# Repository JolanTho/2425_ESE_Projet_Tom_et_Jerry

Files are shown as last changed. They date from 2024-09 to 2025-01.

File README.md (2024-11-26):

# 2425_ESE_Tom&Jerry

## Sommaire
- [Présentation](#présentation)
- [Mécanique](#1-mécanique)
- [Électronique](#2-électronique)
- [Informatique](#3-informatique)
- [Stratégies](#4-stratégies)
- [Installation](#installation)
- [Contribution](#contribution-)
- [Auteurs et Contact](#auteurs-)

---

## Présentation

>Bienvenue sur le dépôt GitHub de **Tom&Jerry**. Ce projet a pour but de développer un robot autonome qui sur un plan plat joue à chat. Le plan est sans rebord, les matchs de 60secondes et le robot change de rôle (Chat/Souris) lors des contacts avec le(s) autre(s) robot(s).

>Ce projet est organisé en trois sous-domaines principaux :
>* **Mécanique** : Conception et fabrication des structures et composants mécaniques.
>* **Électronique** : Conception des circuits électroniques et sélection des composants.
>* **Informatique** : Développement du logiciel et de l'algorithme pour le contrôle du système.
>* **Stratégies** : Focus sur les stratégies mises en place pour s'échapper ou capturer.

---

## Détails du Projet

### 1. Mécanique
>Cette section est dédiée à la conception et à la fabrication des parties mécaniques du projet. 

#### Description :
- **Modélisation CAO** : Les pièces du projet ont été modélisées en utilisant **OnShape**.
- **Matériaux** : Les matériaux utilisés incluent **Plastique PLA, ...**.
- **Assemblage** : Le système est assemblé à l’aide de **(ex. vis, écrous, etc.)** et monté selon les plans fournis dans le dossier **/mechanical_drawings**.

#### Fichiers et Dossiers :
>* **/mechanical_drawings/** : Contient les fichiers CAO et les plans techniques.
>* **/materials_list.txt** : Liste des matériaux et composants utilisés.

---

### 2. Électronique
>Cette partie couvre la conception et le développement des circuits électroniques nécessaires pour alimenter et contrôler le système.

#### Description :
>* **Schémas électroniques** : Conception des circuits avec **Kicad**.
>* **Liste des composants** : Utilisation de microcontrôleurs comme **STM32**, capteurs **TOF, Capteur fin de course, Lidar, IMU, Odom**, et actionneurs **Moteurs de roues**.
>* **PCB** : Un circuit imprimé (PCB) a été conçu pour **Alimentation & Décision du robot**.

#### Fichiers et Dossiers :
>* **electronique/Tom&Jerry_PCB/** : Projet Kicad du PCB principal.
>* **electronique/TOF_PCb/** : Projet Kicad du PCB annexe pour les TOF.
>* **[Read.me ToF](electronique/READMETom&Jerry.md)**
>* **[Read.me Tom&Jerry](electronique/READMETom&Jerry.md)**

---

### 3. Informatique
>Cette section inclut le code source et les algorithmes permettant de contrôler le système.  

#### Description :
>* **Langages utilisés** : Le logiciel a été développé en **C**.  
>* **Architecture logicielle** : L'architecture du programme suit un modèle **/programm_diagramm**.  
>* **Modules et fonctionnalités** : Le logiciel gère **(ex. les capteurs, la communication avec le microcontrôleur, les algorithmes de contrôle**.  

#### Fichiers et Dossiers :
>* **/src/** : Contient le code source du projet.  
>* **/docs/** : Documentation du code et guide d’utilisation.  
>* **/scripts/** : Scripts auxiliaires pour tester ou déployer le logiciel.  
>* **[Read.me](software/README.md)**
---

### 4. Stratégies
>Cette section inclut tout ce qu'il faut savoir sur les stratégies décidées et mis en oeuvre.  

>[!Note]
> Pour faire fonctionner le robot plusieurs stratégies peuvent être mises en place.   
> **Lorsque nous sommes souris**  
>* 1. On fait avancer le robot sur des stratégies prédéfinies et on espère ne pas tomber sur le chat.  
>* 2. On donne des trajectoires aléatoires au robot et on espère ne pas tomber sur le chat ou de la table.  
>* 3. On donne des trajectoires aléatoires en évitant le chat en priant pour ne pas tomber de la table.  
>* 4. On utilise un champ de potentiel pour se repérer et éviter le chat et les bordures.  
>  
> **Lorsque nous sommes Chat**  
>* 1. On fait avancer le robot sur des stratégies prédéfinies et on espère toucher une souris.   
>* 2. On donne des trajectoires aléatoires au robot et on espère toucher une souris sans tomber.  
>* 3. Le Lidar donne l'endroit ou on fonce a pleine balle.  
>* 4. Le lidar donne l'endroit ou on fonce a pleine balle en prenant en compte que l'objectif bouge.   

---

## Installation

### Prérequis :
>[!Important]
>* **Matériel** : La liste du matériel nécessaire ce situe dans le fichier BOM ici, ainsi que dans la partie mécanique ici.
>* **Logiciel** : Nous utilisons STM32 CubeIDE pour programmer notre microcontrolleur. De plus pour la simulation le python est utilisé. 
>* **Connaissance** : Pour comprendre plainement le projet il est nécessaire de maitriser (Kicad, STM32CubeIDE, Onshape). Avec une idée de comment marche les microcontrolleur STM32. (Un ensearque a réussi vous devriez aussi y parvenir).

---

### Instructions :

>[!Tip]
> **Pour utiliser le projet sur un robot**  

1. Cloner le dépôt : 
   ```bash
   git clone https://github.com/JolanTho/2425_ESE_Projet_Tom_et_Jerry.git
   cd projet
   
>[!Tip]
> **Pour utiliser la simulation de champs potentiel**  

1. Cloner le dépôt : 
   ```bash
   git clone https://github.com/JolanTho/2425_ESE_Projet_Tom_et_Jerry.git
   cd projet
---

## Contribution :

---

## Auteurs : 
>* Jolan Thomasset (jolan.thomasset@ensea.fr)  
>* Romain Pace   (romain.pace@ensea.fr)  
>* Rémi Weidle   (remi.weidle@ensea.fr)

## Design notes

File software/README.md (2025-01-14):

# Partie SOFTWARE 

## Sommaire
- [Présentation](#présentation)
- [Architecture](#architecture)
- [Driver-Lidar](#driver-lidar)
- [Driver moteur](#driver-du-zxb5210-driver-moteur)
- [Driver GPIO-Expander](#driver-du-tca9555-gpio-expander)
- [Driver LED](#driver-du-lp5812-driver-led)
- [Driver IMU](#driver-de-ladxl343-imu)

---

## Présentation
>Bienvenue dans la partie développement du projet, dans ce dossier sont présent tous les fichiers de programmation de la STM32. Ceci comprend la configuration de la puce ainsi que les files de projet classique.  

---

## Architecture

```mermaid
stateDiagram-v2
    [*] --> aWait
    aWait --> sideStatus
    USBC_Charge --> Recharge
    LAB_Charge --> Recharge
    aWait --> Recharge
    IMU --> sideStatus
    Recharge --> sideStatus
    Recharge --> [*]
    sideStatus --> Strategie
    sideStatus --> Musique
    Lidar --> Strategie
    CapteurCourant --> Driver
    Driver --> Deplacement
    Moustachex4 --> Deplacement
    Strategie --> Deplacement
    Deplacement --> [*] 
```

## Liste des Tâches du robot

1. **Tâche changeMode_run**
   - **Rôle** : Gère le changement de mode du système.
   - **Priorité** : 1

2. **Tâche lidarTake**
   - **Rôle** : Collecte les données brutes du capteur LiDAR.
   - **Priorité** : 5

3. **Tâche lidarprocess**
   - **Rôle** : Traite les données du LiDAR.
   - **Priorité** : 5

4. **Tâche shell_run**
   - **Rôle** : Fournit une interface en ligne de commande.
   - **Priorité** : 4

5. **Tâche asserv_courant_run** (non active)
   - **Rôle** : Gère l'asservissement en courant des moteurs.
   - **Priorité** : 2

6. **Tâche asserv_position_run** (non active)
   - **Rôle** : Gère l'asservissement en position des moteurs.
   - **Priorité** : 3

---

---

## Driver du Lidar X4

---

### Fonctionnalités principales
- **Démarrage/arrêt** du scan du LiDAR
- **Obtention des informations** sur le capteur (modèle, version firmware, numéro de série)
- **Diagnostic de santé** pour vérifier l'état du capteur
- **Traitement des trames** pour extraire les distances et angles
- **Filtrage et clustering** des données pour détecter des obstacles

---

### Structures de données

#### `LIDAR_device_info_t`
Structure contenant les informations de l'appareil.
```c
typedef struct {
    uint16_t start_sign;
    uint32_t length;
    uint8_t mode;
    uint8_t type_code;
    uint8_t model;
    char firmware[6];
    uint8_t hardware;
    char serial[17];
} LIDAR_device_info_t;
```

#### `LIDAR_health_stat_t`
Structure contenant l'état de santé du LiDAR.
```c
typedef struct {
    uint16_t start_sign;
    uint32_t length;
    uint8_t mode;
    uint8_t type_code;
    uint8_t status_code;
    uint16_t error_code;
} LIDAR_health_stat_t;
```

#### `LIDAR_processing_t`
Structure pour le traitement des données reçues.
```c
typedef struct LIDAR_processing_struct {
    uint8_t frame_buff[FRAME_BUFF_SIZE];
    int point_buff[POINT_BUFF_SIZE];
    uint8_t receive_buff[DATA_BUFF_SIZE];
    int filtred_buff[NB_DEGRES];
    Cluster_t clusters[MAX_CLUSTERS];
    int cluster_cnt;
} LIDAR_processing_t;
```

#### `h_LIDAR_t`
Structure principale du LiDAR.
```c
typedef struct {
    LIDAR_serial_drv_t serial_drv;
    LIDAR_device_info_t device_info;
    LIDAR_health_stat_t health_stat;
    LIDAR_processing_t processing;
    volatile uint8_t rx_flag_uart;
    volatile uint8_t rx_flag_dma;
} h_LIDAR_t;
```

---

### Prototypes des fonctions

#### Fonctions de contrôle
```c
int LIDAR_stop(h_LIDAR_t * h_LIDAR);
int LIDAR_restart(h_LIDAR_t * h_LIDAR);
int LIDAR_get_info(h_LIDAR_t *h_LIDAR);
int LIDAR_get_health_stat(h_LIDAR_t *h_LIDAR);
```

#### Fonctions de traitement des données
```c
int LIDAR_start_scan_dma(h_LIDAR_t *h_LIDAR);
void LIDAR_process_frame(h_LIDAR_t *h_LIDAR, uint8_t *buff);
void medianFilter(h_LIDAR_t *LIDAR);
void find_clusters(h_LIDAR_t *LIDAR);
void kMeansClustering(h_LIDAR_t *LIDAR);
```

---

### Description des fonctions

#### `LIDAR_stop`
Arrête le scan du LiDAR.
- **Entrées** :
  - `h_LIDAR_t *h_LIDAR` : Pointeur vers la structure LiDAR
- **Sorties** :
  - `0` en cas de succès, `-1` en cas d'erreur de transmission, `-2` en cas de timeout

#### `LIDAR_restart`
Redémarre le LiDAR.
- **Entrées** :
  - `h_LIDAR_t *h_LIDAR` : Pointeur vers la structure LiDAR
- **Sorties** :
  - `0` en cas de succès, `-1` en cas d'erreur de transmission

#### `LIDAR_get_info`
Récupère les informations du LiDAR.
- **Entrées** :
  - `h_LIDAR_t *h_LIDAR` : Pointeur vers la structure LiDAR
- **Sorties** :
  - `0` en cas de succès, code d'erreur négatif sinon

#### `LIDAR_get_health_stat`
Récupère l'état de santé du LiDAR.
- **Entrées** :
  - `h_LIDAR_t *h_LIDAR` : Pointeur vers la structure LiDAR
- **Sorties** :
  - `0` en cas de succès, code d'erreur négatif sinon

#### `LIDAR_start_scan_dma`
Démarre le scan en mode DMA.
- **Entrées** :
  - `h_LIDAR_t *h_LIDAR` : Pointeur vers la structure LiDAR
- **Sorties** :
  - `0` en cas de succès, code d'erreur négatif sinon

#### `LIDAR_process_frame`
Traite les trames reçues et extrait les distances et angles.
- **Entrées** :
  - `h_LIDAR_t *h_LIDAR` : Pointeur vers la structure LiDAR
  - `uint8_t *buff` : Buffer contenant les données à traiter

---

### Entrées/Sorties

| Fonction | Entrées | Sorties |
|---|---|---|
| `LIDAR_stop` | `h_LIDAR_t *` | `int` |
| `LIDAR_restart` | `h_LIDAR_t *` | `int` |
| `LIDAR_get_info` | `h_LIDAR_t *` | `int` |
| `LIDAR_get_health_stat`  | `h_LIDAR_t *` | `int` |
| `LIDAR_start_scan_dma` | `h_LIDAR_t *` | `int` |
| `LIDAR_process_frame` | `h_LIDAR_t *`, `uint8_t *` | `void` |
| `medianFilter` | `h_LIDAR_t *` | `void` |
| `find_clusters` | `h_LIDAR_t *` | `void` |
| `kMeansClustering` | `h_LIDAR_t *` | `void` |

---

## Driver du ZXB5210 (Driver Moteur)

---

### Fonctionnalités principales
- **Initialisation** du driver ZXB5210
- **Démarrage/arrêt** du PWM pour la commande des moteurs
- **Contrôle de la vitesse** en avant et en arrière
- **Gestion des angles** pour diriger les moteurs
- **Mise à jour des impulsions** via interruption

---

### Structures de données

#### `MDriver_Config_t`
Structure de configuration pour les moteurs.
```c
typedef struct {
    uint32_t Tim_Channel;        // Canal du timer utilisé
    volatile uint32_t* CCR_Channel; // Pointeur vers le registre CCR
    uint32_t pulseGoal;          // Objectif d'impulsion
    uint32_t offset;             // Offset utilisé pour le calcul de vitesse
} MDriver_Config_t;
```

#### `MDriver_t`
Structure principale du driver moteur.
```c
typedef struct {
    TIM_HandleTypeDef* htim;    // Handle du timer
    MDriver_Config_t* FWD;      // Configuration pour la direction avant
    MDriver_Config_t* REV;      // Configuration pour la direction arrière
    MDriver_Config_t* ACTIVE;   // Direction active actuelle
} MDriver_t;
```

---

### Prototypes des fonctions

#### Fonctions de contrôle
```c
void ZXB5210_init(void);
void ZXB5210_deinit(void);
```

#### Fonctions de gestion de la vitesse
```c
void ZXB5210_speed_FWD(MDriver_t* MDriver, uint8_t alpha);
void ZXB5210_speed_REV(MDriver_t* MDriver, uint8_t alpha);
```

#### Fonctions avancées
```c
void IT_ZXB5210_speed_UPDATE(MDriver_t* MDriver, MDriver_Config_t* SENS);
void ZXB5210_calc_speed(MDriver_Config_t* MDriver_Config, uint32_t initial_Pulse);
void ZXB5210_angle(int angle);
```

---

### Description des fonctions

#### `ZXB5210_init`
Initialise le driver ZXB5210 en configurant les timers et canaux PWM.
- **Entrées** : Aucune
- **Sorties** : Aucune

#### `ZXB5210_deinit`
Arrête le driver ZXB5210 en stoppant les canaux PWM.
- **Entrées** : Aucune
- **Sorties** : Aucune

#### `ZXB5210_speed_FWD`
Configure la vitesse du moteur en mode avant.
- **Entrées** :
  - `MDriver_t* MDriver` : Pointeur vers la structure du driver moteur
  - `uint8_t alpha` : Pourcentage de la vitesse souhaitée (0 à 100)
- **Sorties** : Aucune

#### `ZXB5210_speed_REV`
Configure la vitesse du moteur en mode arrière.
- **Entrées** :
  - `MDriver_t* MDriver` : Pointeur vers la structure du driver moteur
  - `uint8_t alpha` : Pourcentage de la vitesse souhaitée (0 à 100)
- **Sorties** : Aucune

#### `IT_ZXB5210_speed_UPDATE`
Met à jour les impulsions de vitesse via interruption.
- **Entrées** :
  - `MDriver_t* MDriver` : Pointeur vers la structure du driver moteur
  - `MDriver_Config_t* SENS` : Pointeur vers la configuration de la direction active
- **Sorties** : Aucune

#### `ZXB5210_calc_speed`
Calcule et ajuste la vitesse en fonction des impulsions.
- **Entrées** :
  - `MDriver_Config_t* MDriver_Config` : Pointeur vers la configuration du moteur
  - `uint32_t initial_Pulse` : Nombre initial d'impulsions
- **Sorties** : Aucune

#### `ZXB5210_angle`
Permet de contrôler les deux moteurs pour orienter le robot selon un angle donné.
- **Entrées** :
  - `int angle` : Angle souhaité (0 à 360 degrés)
- **Sorties** : Aucune

---

### Entrées/Sorties

| Fonction | Entrées | Sorties |
|---|---|---|
| `ZXB5210_init` | Aucune | Aucune  |
| `ZXB5210_deinit` | Aucune | Aucune  |
| `ZXB5210_speed_FWD` | `MDriver_t*`, `uint8_t` | Aucune  |
| `ZXB5210_speed_REV` | `MDriver_t*`, `uint8_t` | Aucune  |
| `IT_ZXB5210_speed_UPDATE`  | `MDriver_t*`, `MDriver_Config_t*` | Aucune  |
| `ZXB5210_calc_speed` | `MDriver_Config_t*`, `uint32_t` | Aucune  |
| `ZXB5210_angle` | `int` | Aucune  |

---

## Driver du TCA9555 (GPIO Expander)

---

### Fonctionnalités principales
- **Initialisation** du GPIO expander TCA9555
- **Lecture et écriture** des registres du TCA9555 via I2C
- **Configuration des ports** en entrée ou sortie
- **Gestion des inversions de polarité** sur les ports

---

### Structures de données

#### `GPIOExpanderRegister_t`
Structure représentant un registre du GPIO expander.
```c
typedef struct {
    char* name;   // Nom du registre
    uint8_t reg;  // Adresse du registre
} GPIOExpanderRegister_t;
```

---

### Prototypes des fonctions

#### Fonctions principales
```c
void TCA9555_init(void);
HAL_StatusTypeDef TCA9555_WriteRegister(uint8_t reg, uint8_t data);
HAL_StatusTypeDef TCA9555_ReadRegister(uint8_t reg, uint8_t* recptData, uint8_t lenData);
```

---

### Description des fonctions

#### `TCA9555_init`
Initialise le GPIO expander TCA9555 en configurant les registres de configuration et de polarité.
- **Entrées** : Aucune
- **Sorties** : Aucune
- **Détails** :
  - Configure les ports 0 et 1 en entrée ou sortie.
  - Lit et affiche la valeur initiale des registres de l’expander.

#### `TCA9555_WriteRegister`
Écrit une valeur dans un registre du GPIO expander.
- **Entrées** :
  - `uint8_t reg` : Adresse du registre à écrire
  - `uint8_t data` : Donnée à écrire dans le registre
- **Sorties** :
  - `HAL_StatusTypeDef` : Statut de la transmission I2C

#### `TCA9555_ReadRegister`
Lit une valeur à partir d’un registre du GPIO expander.
- **Entrées** :
  - `uint8_t reg` : Adresse du registre à lire
  - `uint8_t* recptData` : Pointeur pour recevoir les données lues
  - `uint8_t lenData` : Nombre d’octets à lire
- **Sorties** :
  - `HAL_StatusTypeDef` : Statut de la transmission I2C

---

### Entrées/Sorties

| Fonction | Entrées | Sorties |
|---|---|---|
| `TCA9555_init` | Aucune | Aucune |
| `TCA9555_WriteRegister` | `uint8_t`, `uint8_t` | `HAL_StatusTypeDef` |
| `TCA9555_ReadRegister` | `uint8_t`, `uint8_t*`, `uint8_t` | `HAL_StatusTypeDef` |

---

## Driver du LP5812 (Driver LED)

---

### Fonctionnalités principales
- **Initialisation** du pilote de LED LP5812
- **Lecture et écriture** des registres 16 bits du LP5812 via I2C
- **Configuration des LEDs** en mode direct drive
- **Contrôle de l'intensité lumineuse** des LEDs

---

### Prototypes des fonctions

#### Fonctions principales
```c
void LP5812_Init(void);
HAL_StatusTypeDef LP5812_WriteRegister(uint16_t reg_addr, uint8_t data);
HAL_StatusTypeDef LP5812_ReadRegister(uint16_t reg_addr, uint8_t *pData);
```

---

### Description des fonctions

#### `LP5812_Init`
Initialise le pilote de LED LP5812 en configurant les différents registres pour activer les LEDs et régler l'intensité.
- **Entrées** : Aucune
- **Sorties** : Aucune
- **Détails** :
  - Active le composant en mettant le bit `chip_en` à 1.
  - Configure le mode de commande des LEDs en mode direct drive.
  - Initialise les registres pour contrôler les 12 LEDs avec une intensité prédéfinie.
  - Envoie une commande de mise à jour pour valider la configuration.

#### `LP5812_WriteRegister`
Écrit une valeur dans un registre 16 bits du LP5812.
- **Entrées** :
  - `uint16_t reg_addr` : Adresse 16 bits du registre à écrire
  - `uint8_t data` : Donnée à écrire dans le registre
- **Sorties** :
  - `HAL_StatusTypeDef` : Statut de la transmission I2C

#### `LP5812_ReadRegister`
Lit une valeur à partir d’un registre 16 bits du LP5812.
- **Entrées** :
  - `uint16_t reg_addr` : Adresse 16 bits du registre à lire
  - `uint8_t *pData` : Pointeur pour recevoir la donnée lue
- **Sorties** :
  - `HAL_StatusTypeDef` : Statut de la transmission I2C

---

### Entrées/Sorties

| Fonction | Entrées | Sorties |
|---|---|---|
| `LP5812_Init` | Aucune | Aucune |
| `LP5812_WriteRegister` | `uint16_t`, `uint8_t` | `HAL_StatusTypeDef` |
| `LP5812_ReadRegister` | `uint16_t`, `uint8_t*` | `HAL_StatusTypeDef` |

---

## Driver de l'ADXL343 (IMU)

---

### Fonctionnalités principales
- **Initialisation** de l'accéléromètre ADXL343
- **Lecture et écriture** des registres via I2C
- **Acquisition des données d'accélération** sur les axes X, Y et Z
- **Calibration** automatique pour compenser les offsets

---

### Structures de données

#### `XYZ_t`
Structure contenant les valeurs d'accélération sur les trois axes.
```c
typedef struct {
    float X; // Accélération sur l'axe X en mm/s²
    float Y; // Accélération sur l'axe Y en mm/s²
    float Z; // Accélération sur l'axe Z en mm/s²
} XYZ_t;
```

#### `IMURegister_t`
Structure représentant un registre de l'IMU.
```c
typedef struct {
    char *name;   // Nom du registre
    uint8_t reg;  // Adresse du registre
} IMURegister_t;
```

---

### Prototypes des fonctions

#### Fonctions principales
```c
void ADXL343_init(void);
HAL_StatusTypeDef ADXL343_WriteRegister(uint8_t reg, uint8_t data);
HAL_StatusTypeDef ADXL343_ReadRegister(uint8_t reg, uint8_t* pData, uint8_t lenData);
XYZ_t ADXL343_getAcc(void);
```

---

### Description des fonctions

#### `ADXL343_init`
Initialise l'accéléromètre ADXL343 en configurant les différents registres.
- **Entrées** : Aucune
- **Sorties** : Aucune
- **Détails** :
  - Configure les registres de seuil, durée, latence et axes pour les détections de tap.
  - Active les interruptions pour les détections de tap et d'activité/inactivité.
  - Initialise le mode de puissance et le format des données.
  - Effectue une calibration automatique sur les trois axes.

#### `ADXL343_WriteRegister`
Écrit une valeur dans un registre du ADXL343.
- **Entrées** :
  - `uint8_t reg` : Adresse du registre à écrire
  - `uint8_t data` : Donnée à écrire dans le registre
- **Sorties** :
  - `HAL_StatusTypeDef` : Statut de la transmission I2C

#### `ADXL343_ReadRegister`
Lit une valeur à partir d’un registre du ADXL343.
- **Entrées** :
  - `uint8_t reg` : Adresse du registre à lire
  - `uint8_t* pData` : Pointeur pour recevoir les données lues
  - `uint8_t lenData` : Nombre d’octets à lire
- **Sorties** :
  - `HAL_StatusTypeDef` : Statut de la transmission I2C

#### `ADXL343_getAcc`
Récupère les données d'accélération sur les trois axes.
- **Entrées** : Aucune
- **Sorties** :
  - `XYZ_t` : Structure contenant les valeurs d'accélération sur les axes X, Y et Z en mm/s²
- **Détails** :
  - Lit les registres de données X, Y et Z.
  - Applique un filtrage simple pour ignorer les petites variations.

---

### Entrées/Sorties

| Fonction | Entrées | Sorties |
|---|---|---|
| `ADXL343_init` | Aucune | Aucune |
| `ADXL343_WriteRegister` | `uint8_t`, `uint8_t` | `HAL_StatusTypeDef` |
| `ADXL343_ReadRegister` | `uint8_t`, `uint8_t*`, `uint8_t` | `HAL_StatusTypeDef` |
| `ADXL343_getAcc` | Aucune | `XYZ_t` |

---
## Shell
>  Afin de pouvoir effectuer des tests unitaire le plus facilement possible nous avons décider d'utiliser un shell. Nous avons donc créer des fonctions pour tester les moteurs, pour vérifier le foncionement correct de l'ADXL ainsi que tester le LIDAR.
### Help
> Cette fonction permet d'ébumérer toutes les fonction présente dans le shell.
### Clear 
> Permet de supprimé toutes les actions effectué précédement sur l'écran.
### Start
> Permet de faire démarrer le robot.
### Stop
> Permet d'arrêter le robot.
### Speed 
> Permet de faire varier la vitesse des moteurs en controlant indépendament chaque moteur.
### Angle
> Permet de dire au robot à quel angle on détecte un peu et ansi vérifier si celui-ci s'orinte bien en face de l'objet détecté.
### CS
>
### LED
> Permet de changer les paramètre des LEDs pour créer notament des chenillards.
### imu
>
### imusf
> Permet de tester si l'IMU fonctionne correctement.
### imuu
> Permet d'envoyer une demande de lecture à un registre précis de l'IMU.
### imug
> Permet de récupérer la valeur de l'accélération.
### adc
> Permet de démarrer l'asservissement en courant.
### Lidar
> Permet de démarrer le LIDAR.
### miaou
> Active le DAC pour faire du son et que le robot fasse "miaou".
### reset
> Permet de reset le robot en cas de disfonctionnement.
___

## Auteurs : 
>* Jolan Thomasset (jolan.thomasset@ensea.fr)  
>* Romain Pace   (romain.pace@ensea.fr)  
>* Rémi Weidle   (remi.weidle@ensea.fr)

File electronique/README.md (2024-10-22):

# Partie éléctronique 

## Sommaire
- [Présentation](#présentation)
- [Alimentation](#alimentation)
- [Driver Moteurs](#drivers-moteurs)
- [STM32](#stm32)
- [Peripheriques](#périphériques)
- [Peripherique Annexe](#périphériques-annexes)
- [Musique](#musique)

---

## Présentation
>Bienvenue dans la partie éléctronique du projet, dans ce dossier sont présent tous les fichiers de conception du PCB KiCad ainsi que tous les fichiers de fabrications Gerber.  
Deux fichiers sont actuellement dans le directory. Tom&Jerry_PCB pour le PCB principal et TOF_PCB pour le secondaire.   
Il est détaillé chaque composante du Schématique/PCb dans ce Read.me  

---

## Alimentation
>[!Tip]
>Pour notre robot nous utilisons plusieurs système pour gérer le circuit d'alimentation. On a entre autre un BMS ( Batterie système management ), ainsi qu'un pseudo Power Path Management. La batterie utilisée est la suivante : [here](../datasheet/Batterie.pdf)  

>[!Tip]
>Des connecteurs Pac-Man sont utilisés au niveau de la recharge de batterie afin de pouvoir déconnecter facilement le circuit de charge si il est foireux. De plus un interrupteur est ajouté pour allumer/Eteindre le robot ainsi qu'un fusible pour protéger des surcourants sur la batterie.  

**Recharge de batterie**

[Recharge](../screenshot/electronique/usbC.png)

>Pour la recharge de la batterie nous prévoyons deux connecteurs : Type-C et Bornier afin de pouvoir recharger la batterie par alimentation stabilisée de labo ainsi que par cable USB-C (Plus difficile à mettre en oeuvre) [Documentation1](../datasheet/PPM_BMS.pdf).  

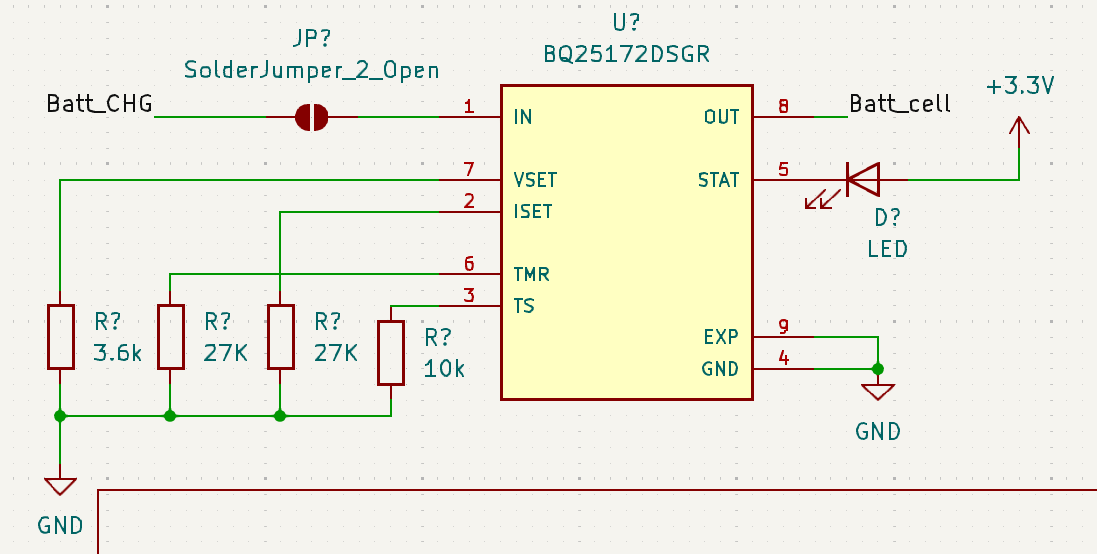
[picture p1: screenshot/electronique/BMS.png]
  

>[!Note]
>Cette entrée d'energie est gérée par le **BMS [BQ25172DSGR](../datasheet/BQ25172.pdf) de TI**. Celui-ci est cablé tel quel :  
>* IN : Entrée de tension de charge de batterie. Max 0.8 A (Cf : Doc)  
>* VSET : Programme le nombre de cellule --> 6 cellules + Charge intermittente  
>* ISET : Programme le courant de charge --> 0.8A   
>* TMR : Programme le Timer de sureté --> 6Hr  
>* TS : Programme la température de sureté de charge --> Donnée constructeur    
>* OUT : Sortie de tension de charge de la batterie  
>* STAT : Sortie d'indication de l'état de charge à drain ouvert  
>* EXP : Ground (Pad thermique)  
>* GND : Ground  

[CanalP](../screenshot/electronique/canalP.png)

>On a un transistor à canal P pour bloquer la charge du circuit par batterie lorsqu'une tension vient du bornier ou de l'USB-C. De plus on ajoute des condensateur (C...) pour eviter les retours de courant dû a des freinage des roues dans la résistance et donc dans l'alimentation derrière [(Doc)](../datasheet/slua376.pdf).    

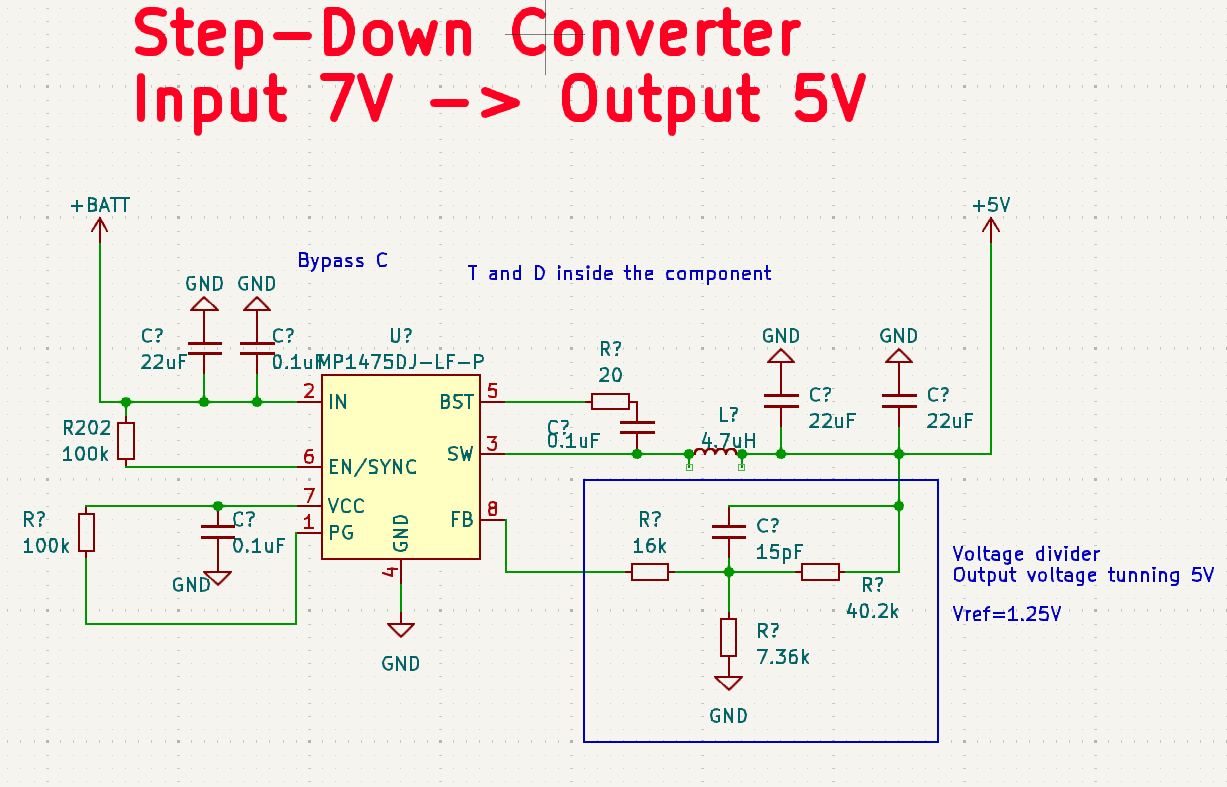
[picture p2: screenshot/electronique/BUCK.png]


>On utilise un premier convertisseur Buck pour abaisser la tension à 5V. Celui-ci est à découpage donc plus cher mais possède un meilleur rendement et un plus faible échauffement. Cela est parfait puisqu'il alimente le lidar ainsi que tous les circuits 3.3v derrière et donc peut avoir des appels de courant assez élevé (Comme démarrage de lidar).  

>[!Note]
>**Convertisseur Buck ([MP1475](../datasheet/MP1475.pdf))**  
>* IN : Tension d'entrée  
>* BST : Bootstrap  
>* SWT : Sortie de commutation  
>* PG : Sortie de puissance  
>* VCC : LDO interne de 5v  
>* EN/SYNC : Pour les clocks externes  
>* FB : Feedback  
>* GND : Ground  

>Actuellement les données sont celle ce la doc. La seule chose réglée est le pont diviseur avec une Vref = 1.25V pour avoir une sortie de 5V en sortie.  

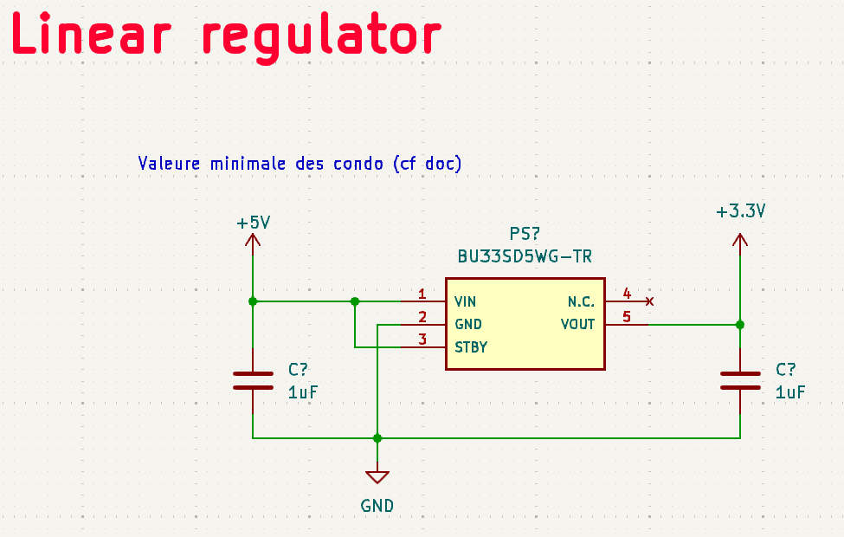
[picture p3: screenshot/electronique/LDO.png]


>Simple convertisseur linéaire qui abaisse de 5V vers 3.3V pour alimenter certains capteurs ou encore la STM32 qui n'accepte pas du 5V. L'utilisation d'un buck serai plus utile si on recherche la performance cependant un LDO est suffisant car moins couteux, plus simple à mettre en place. L'abaissement de tension est faible sur de faible courants par conséquent la dissipation thermique sera faible ce qui justifie un LDO plutôt qu'un buck.  

>[!Note]
>**Convertisseur LDO [(BU33SD5WG-TR)](../datasheet/buxxsd5wg-e.pdf)**  
>* VIN : Tension d'entrée  
>* GND : Ground  
>* STBY : StandBy --> Ici sur High il marche dés qu'il est alimenté.   
>* N. C. : No Connected pin  
>* Vout : Tension de sortie  

---

## Drivers moteurs
>Afin de pouvoir mouvoir le robot sur la table de jeu, nous utilisons des moteurs type MCC (DfRobot FIT0520). Ces moteurs possèdent des codeurs déjà sur l'arbre moteur ce qui a l'avantage de ne négliger aucun décalage entre une roue de codeur et la roue de l'arbre moteur. Cependant si jamais la roue patine ou glisse le codeur ne prendra pas en compte ce dérapage ce qui entrainera des erreurs. Il faut donc impérativement que la mécanique permette au robot de rester particulièrement stabilisé sur le sol.  

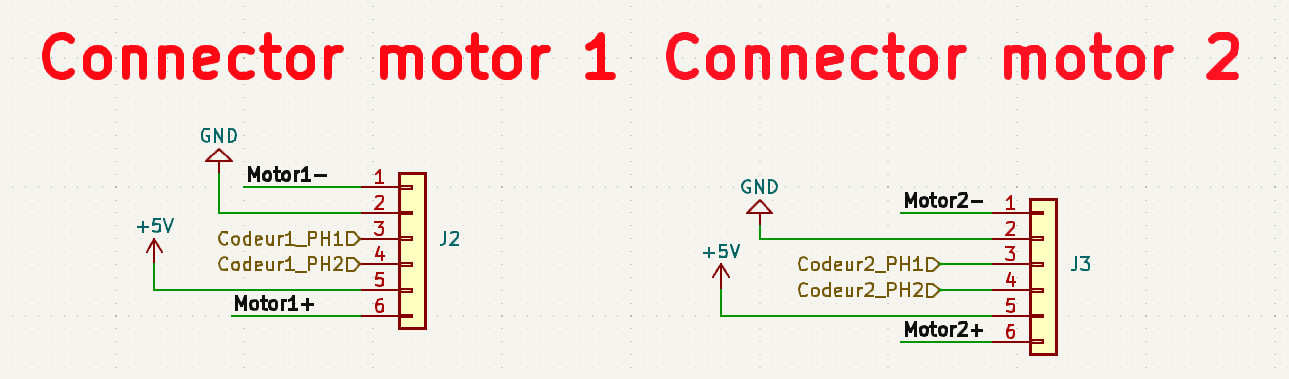
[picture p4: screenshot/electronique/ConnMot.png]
Connecteur Moteur


>[!Note]
>Branché sur la carte les deux moteurs auront de beaux JST-XH de 6 Pins chacun tels que :  
>* Motor - : Phase - du moteur  
>* Motor + : Phase + du moteur  
>* GND : Ground   
>* 5V : Alimentation des codeurs en 5V   
>* Codeur PH1 : Pin allant avec PH2 avec la trame du codeur pour déterminer ensuite la vitesse du robot.   
>* Codeur PH2 : Pin allant avec PH1 avec la trame du codeur pour déterminer ensuite la vitesse du robot.   

>Pour controler ces deux moteurs chaque moteur aura son driver.   

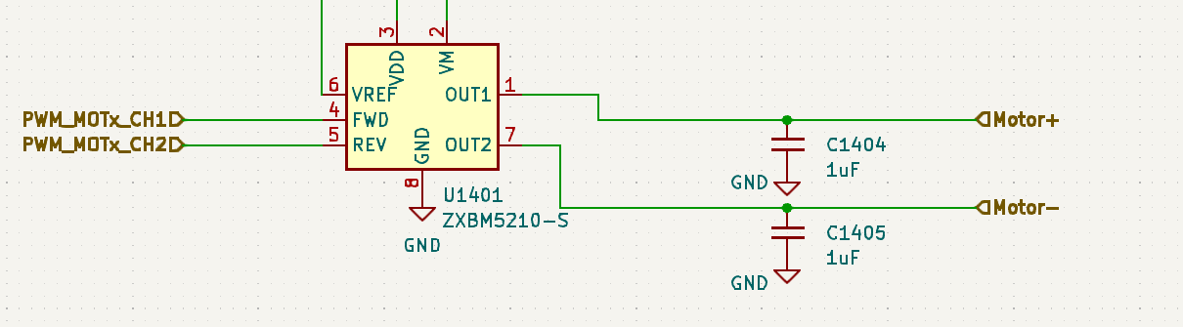
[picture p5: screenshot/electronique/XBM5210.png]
Driver Moteur


>[!Note]
>**Driver [ZXBM5210](../datasheet/ZXBM5210.pdf)**  
>* Vref : Tension de référence pour setup l'oscillator PWM du composant.   
>* VDD : Alimentation du composant en 5V   
>* VM : Tension d'alimentation des moteurs  
>* FWD : PWM pour faire avancer le robot  
>* REV : PWM pour faire reculer le robot  
>* Out 1 :  Sortie au moteur phase -  
>* Out 2 : Sortie au moteur phase +  

>[!Important]
>Il est à noter que des capa de découplage sont utilisés afin d'éviter les fluctuation de courant trop rapide sur Vref ( Car tension de référence), sur les phases du moteur afin d'éviter des signaux créneau pur. De plus la documentation suggère un système de diode afin d'éviter la réversibilité du courant vers la batterie. Celui-ci ne sera pas utilisé afin d'éviter de cramer des diodes suite à des quantités trop importantes de courant que se déchargeraient dans les diodes.   

>[!Tip]
>En plus de cela nous utilisons un composant pour mesurer le courant drainé de la batterie vers les moteurs à l'aide d'une résistance dite shunt. Ce composant permettra de nous aider à asservir pourquoi pas en courant mais aussi de protection afin d'éviter comme nous n'avons pas mis les diodes d'avoir des données sur ce qui se passe.  

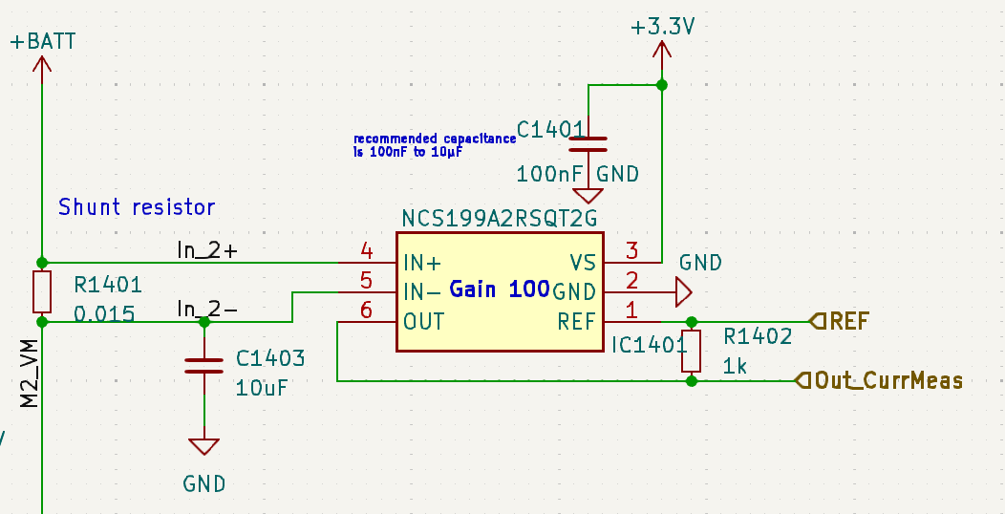
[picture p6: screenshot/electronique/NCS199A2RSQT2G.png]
Mesureur de courant


>[!Note]
>**Mesureur de courant [NCS199A2RSQT2G](../datasheet/NCS199A2RSQT2G.pdf)**  
>* GND : Ground  
>* In + : Entrée + coté résistance de shunt pour capter le courant  
>* In - : Entrée - coté résistance de shunt pour capter le courant  
>* Vs : Tension d'alimentation du composant  
>* Vref : Tension de référence dont je ne sais pas à quoi elle sert (J'ai cable comme la doc)  
>* Out : Sortie du composant avec ke courant prêt à être lu par un ADC  

>Comme toute entrée de composant celui-ci ne fait pas l'impasse une capacité de découplage a été ajoutée. De plus la résistance de 1kOhm a été mise pour préparer l'entrée du courant dans l'ADC conforme à la documentation.  

---

## STM32 
>[!Important]
>Avant de développer sur la STM32 et la facon dont nous avons répartis les pins de celle-ci. Pour que celle-ci fonctionne correctement nous utiliserons un quartz externe pour cadencer la STM32 (Configuré dans l'IOC de STM32CubeIDE). 

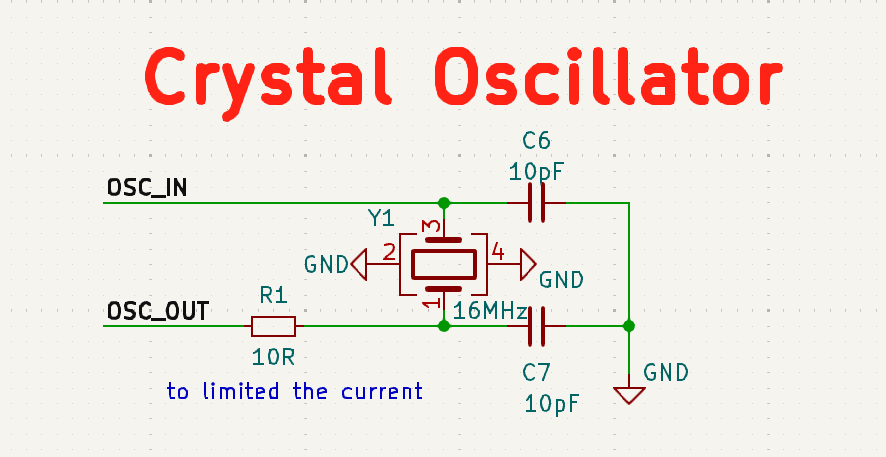
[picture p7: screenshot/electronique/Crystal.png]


>[!Important]
>De plus nous utilisons une connexion STLink pour le debug de la carte via PC. 

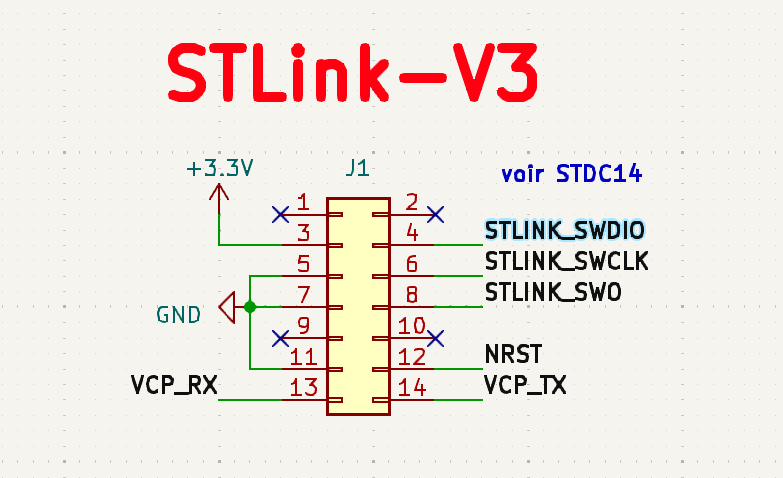
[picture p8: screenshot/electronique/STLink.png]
STLink


---

## Périphériques 

>[!Note]
>La carte actuelle va gérer certains capteurs. Avec ceux-ci le robot pourra (Nous l'esperons) se repérer sur la table et réaliser au mieux la stratégie mise en place. 

>[!Tip]
> Afin de détecter les bords nous avons décider de faire de la redondance. En effet nous utilisons des capteurs "Moustache" ainsi que TOF pour repérer les bords de la table et éviter que les robots tombent. L'avantage des capteurs moustache est qu'ils sont mécanique donc fiable maintenant cela demande de na pas louper son intégration sur la base roulante ce qui n'es tpas gagner. Pour cela nous pouvvons utiliser les TOF. Ceux-ci sont plus simple à positionner sur le robot et à fonctionner. Cependant l'exploitation des données est plus dure (I2C + GPIO Extender...). 

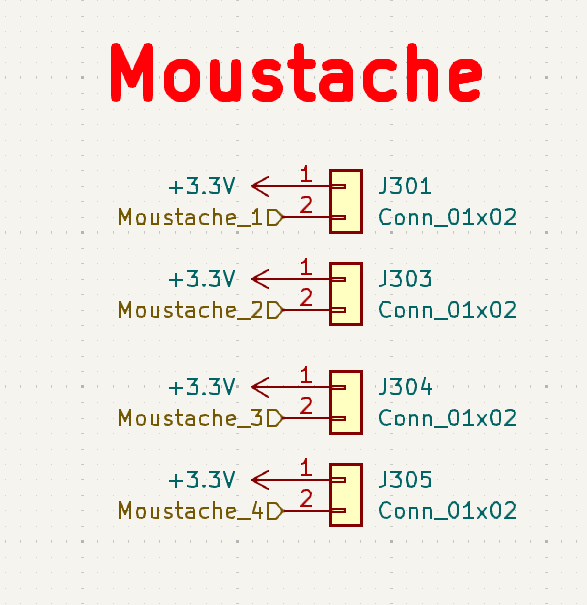
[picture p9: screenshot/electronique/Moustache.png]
Moustache


>[!Note]
>Branché sur la carte les quatre capteurs moustahce ont un JST  :  
>* 3.3V : Alimentation
>* GND : Ground  
>Ceux-ci marchent en interrupteur pas besoin de plus de chose pour lire leurs données. 

TOF

>[!Note]
>**Capteurs TOF [VL53L1X](../datasheet/VL53L1X.pdf):**   
>* AVDDVCSEL : VCSEL tension d'alimentation  
>* AVSSVCSEL : VCSEL Ground    
>* GND1 - GND4 : Ground  
>* XShut: Pin pour shutdown le composant. celui-ci est actif sur un signal Bas  
>* GPIO1 : GPIO pour gérer les interruptions  
>* DNC : A ne pas connecter (Doit être floating)  
>* SDA : Serial data bus
>* SCL : Serial clock bus
>* AVDD : Tension d'alim du composant
>Ceux-ci sont sur les cartes fournient avec produit par STM32. 

>[!Note]
>En plus de la détection de bord avec les TOF et les capteurs "Moustache", le robot aura un IMU pour faire de la fusion de donnée (Rédigé en septembre ca ne sera pas traité pas assez de temps) ainsi que de vérifier si un robot nous touche. De plus il y aura un lidar pour détecter les robots sur la table et foncer sur eux. 

Lidar

>[!Note]
>**Capteurs TOF [YDLidar X2](../datasheet/YDLIDARX2.pdf):**    
>* M_CTR : Entrée de la PWM du moteur du Lidar    
>* TX : Sortie UART avec les données du LIDAR      
>* GND : Ground    
>* VCC : Tension d'alimentation du lidar (5v)  

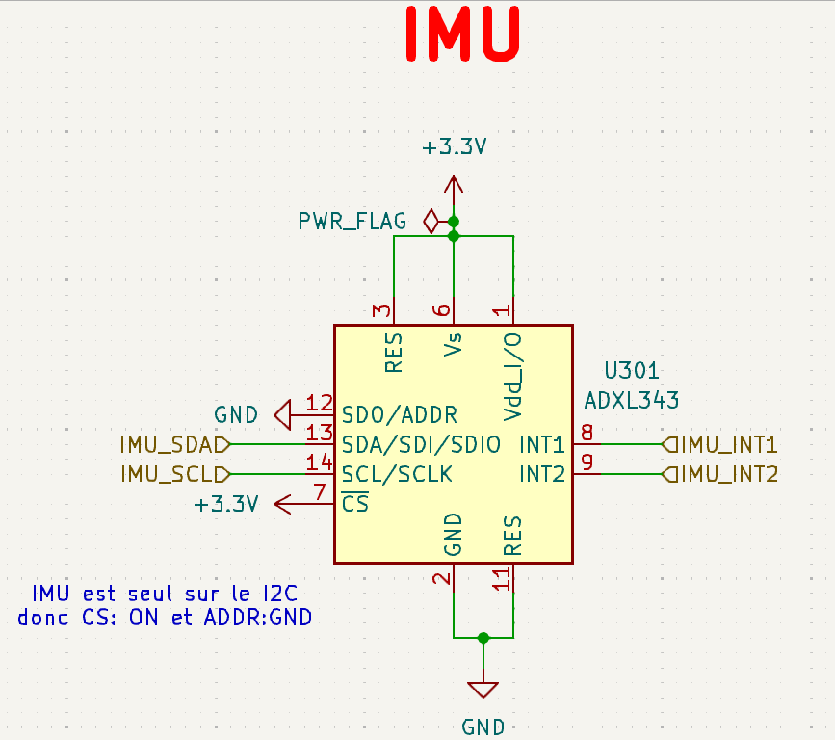
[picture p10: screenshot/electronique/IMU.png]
IMU
 

>[!Note]
>**IMU [ADXL343](../datasheet/ADXL343.pdf):**   
>* Vs : Tension d'alimentation du composant   
>* GND : Ground   
>* VDD : Tension d'alimentation de l'interface digitale  
>* SDA : Serial data bus  
>* SCL : Serial clock bus  
>* SDO : I2C adresse  
>* NC : A garder non connecte  
>* Int1 - Int2 : Pin d'interruption   
>* CS : Chip Select

---

## Périphériques Annexes 
>Deux composants non imposés ont été utilisés en plus de ceux imposés afin de pouvoir tout connecter à la STM32. Suite à la solution technique des TOF employé le nombre de GPIO recquis a quelque peu explosé surpassant la capacité de la STM. par conséquent un GPIO Extender est utilisé pour ajouter des GPIO afin de couper et utiliser les TOF lorsque nous en avons besoin.   

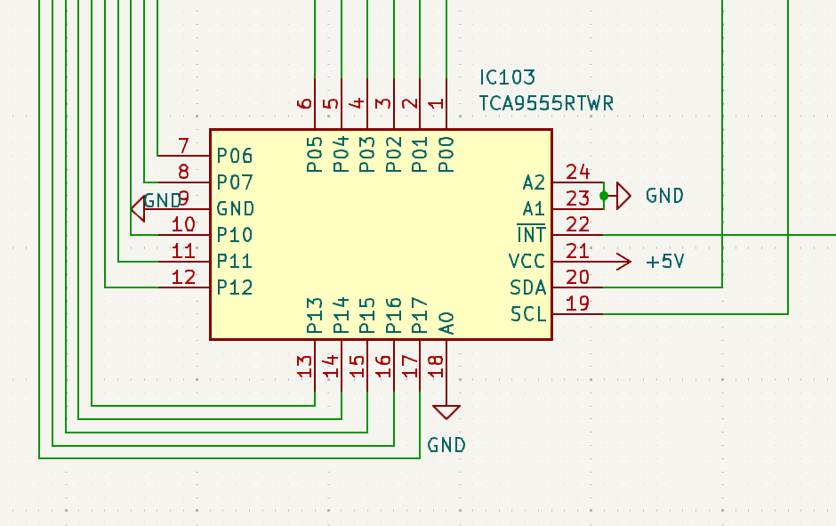
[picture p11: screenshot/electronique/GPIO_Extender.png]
GPIO Extender


>[!Note]
>**GPIO Extender [TCA9555RTWR](../datasheet/TCA9555.pdf)**  
>* A0 : Adress Input 0  
>* A1 : Adress Input 1  
>* A2 : Adress Input 2  
>* GND : Ground   
>* P00 à P17 : P/port I/O connecte comme Input au démarrage.   
>* SCL : Serial clock bus  
>* SDA : Serial data bus  
>* VCC : Tension d'alimentation du composant  
>* INT : Permet de donner des interruptions avec une Pull-Up resistance.   

>[!Tip]
>En plus de ce composant nous avons utilisé un petit composant pour traiter nos leds. En effet en comptant 4 de débugs, robot allumé, chat/souris,... Nous nous sommes sentis à l'étroit et avons décidé de rajouter un composant qui drive 4 RGB. Cela sera parfait pour débug et montrer les informations nécessaires.  

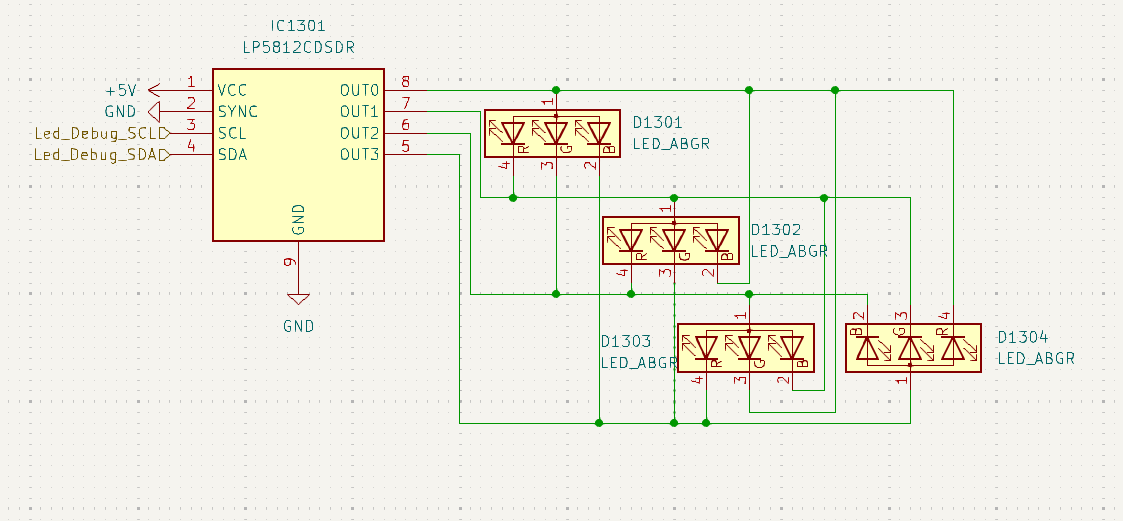
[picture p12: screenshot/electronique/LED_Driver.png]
RGB Led Driver


>[!Note]
>**RGB LED Driver [LP5812CDSDR](../datasheet/LP5812.pdf)**  
>* VCC : Tension d'alimentation du composant  
>* GND : Ground  
>* SYNC : Synchro du composant sur GND (C'est la doc je sais pas pk)  
>* SCL : Serial clock bus  
>* SDA : Serial data bus   
>* OUT0 - OUT3 : Sorties vers les LED   

>Pour ce composant nous verrons pour le faire marcher en temps voulu avec le SPI pour allumer nos LEDS. Celles-ci sont cablés comme décrit dans la documentation.   

---

## Musique 
>Ayant dans notre groupe notre jolan nationnal, le projet ne pouvait être correctement réalisé sans l'ajout de bout de musique sur le robot. Pour se faire les sorties DAC de la STM32 dédiées seront utilisées. Ce signal audio sera amplifié par un amplificateur de Classe D puis va être envoyé dans des hauts parleurs.   

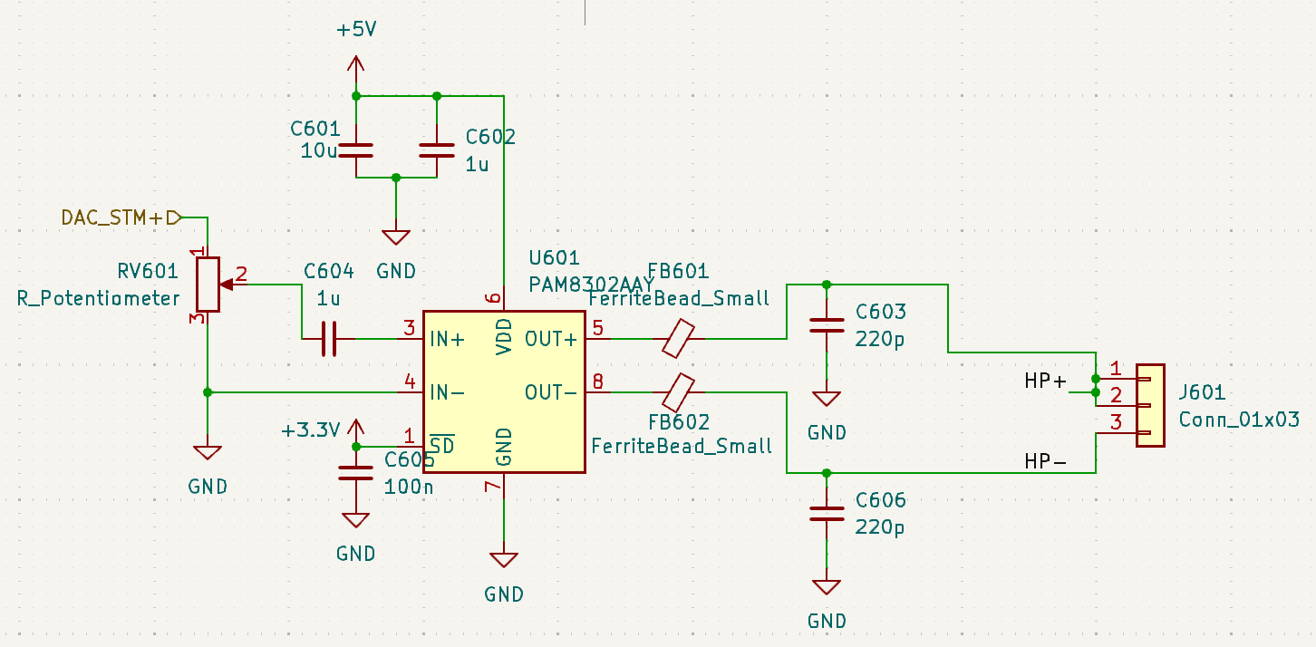
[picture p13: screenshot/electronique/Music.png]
Musique


>[!Note]
>**Ampli de Classe D [PAM8302AAY](../datasheet/PAM8302A.pdf)**  
>* IN + : Entrée DAC  +  
>* IN - : Entrée DAC  -   
>* SD : Doit rester sur HIGh pour éviter qu'il soit shutdown (donc relié à 3.3v)  
>* VDD : Alimentation du composant  
>* OUT + : Sortie + du haut parleur   
>* OUT - : Sortie - du haut parleur  

>[!Important]
>Les deux capacité de découplage ainsi que les deux ferrites sont celles conforme à la documentation afin de réduire les interférence electromagnétique à partir de 1MHz et au dela. Ceci est parfait puisque ce composant est à coté de composant sensible comme la STM...  

## Auteurs : 
>* Jolan Thomasset (jolan.thomasset@ensea.fr)  
>* Romain Pace   (romain.pace@ensea.fr)  
>* Rémi Weidle   (remi.weidle@ensea.fr)

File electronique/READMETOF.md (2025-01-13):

# Partie éléctronique TOF

## Sommaire

---

## Présentation
>Bienvenue dans la partie éléctronique du projet, dans ce dossier sont présent tous les fichiers de conception du PCB KiCad ainsi que tous les fichiers de fabrications Gerber.  
Deux projets sont actuellement dans le directory. Tom&Jerry_PCB pour le PCB principal et TOF_PCB pour le secondaire.   
Il est détaillé chaque composante du Schématique/PCb des TOF dans ce ReadMe. Sinon pour le principal aller [ici](READMETom&Jerry.md)

---

## Contexte 
>Pour pouvoir respecter la contrainte pour laquelle le robot ne doit pas tombé nous avons choisis deux solutions techniques la première est d'utiliser des capteurs moustaches positionné à l'avant et à l'arrière du robots. La deuxième solution est d'utiliser des TOF (Time of Flight). Pour pouvoir les fixer aux robots nous avons fais des pièces en 3D qui seront présenté dans le ReadMe consacré à la mécanique.

---
## Solution technique
>Nous avons choisi d'utiliser 6 TOF, 3 à l'avant du robot et 3 à l'arrièere. Nous avons donc fais 6 PCB pour pouvoir relier nos capteur TOF au PCB principale. Le PCB fixé au capteur TOF centrale est relié au PCB principal et ensuite celui-ci est relié au deux autres PCB.

```mermaid
---
config:
  flowchart:
    htmlLabels: false
  layout: fixed
---
flowchart LR
    n2["PCB central"] --> n1["PCB gauche"] & n3["PCB droite"]
    n4["PCB prinipal"] --> n2
    n2@{ shape: rounded}
    n1@{ shape: rounded}
    n3@{ shape: rounded}
    n4@{ shape: rounded}
    style n2 stroke:#000000
    style n1 stroke:#000000
    style n3 stroke:#000000
    style n4 stroke:#000000
```
>Les PCB fabriqué sont des PCB deux couches qui ont été fabriqué à l'ENSEA.

## PCB
| PCB gauche | PCB central  | PCB droit |
| --- | --- |---|
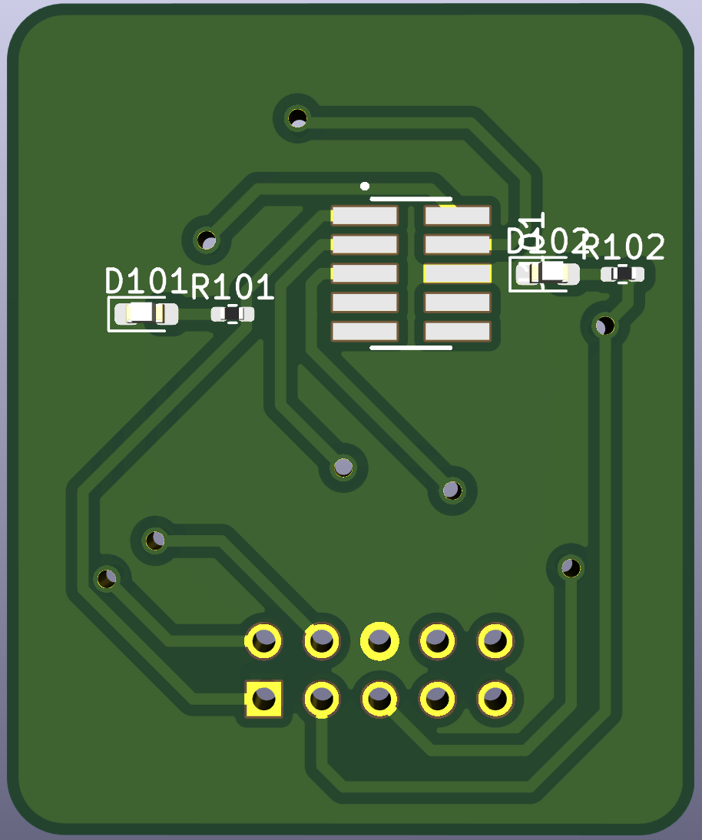
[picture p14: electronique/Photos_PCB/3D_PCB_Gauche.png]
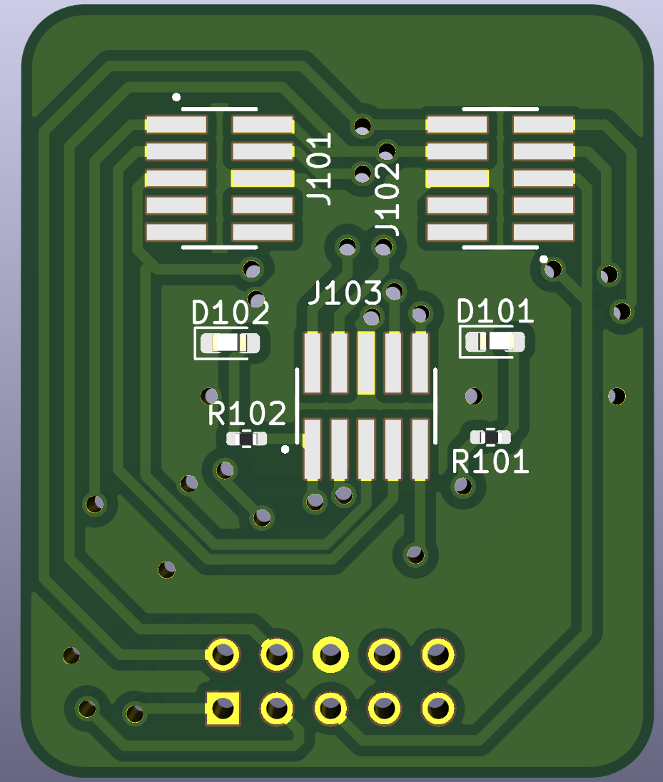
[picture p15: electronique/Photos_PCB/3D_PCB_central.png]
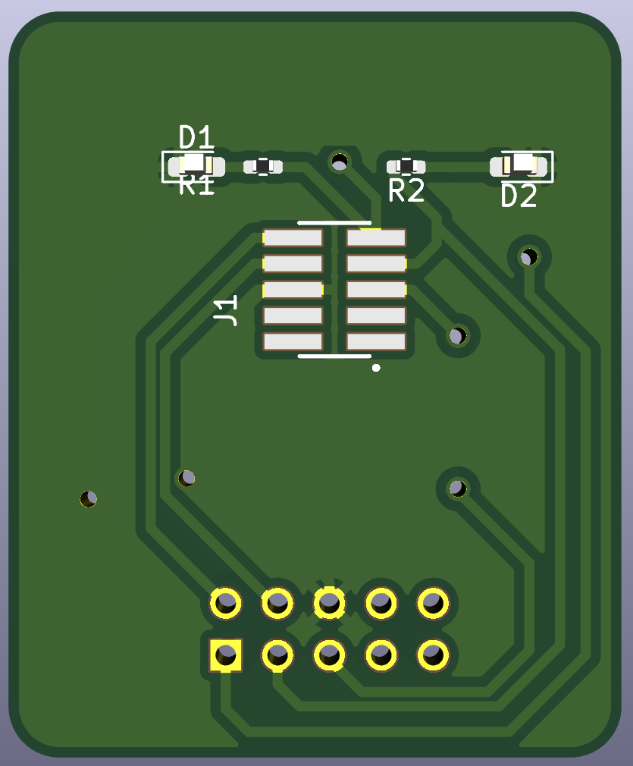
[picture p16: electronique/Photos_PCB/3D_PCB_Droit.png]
|   |   |   |
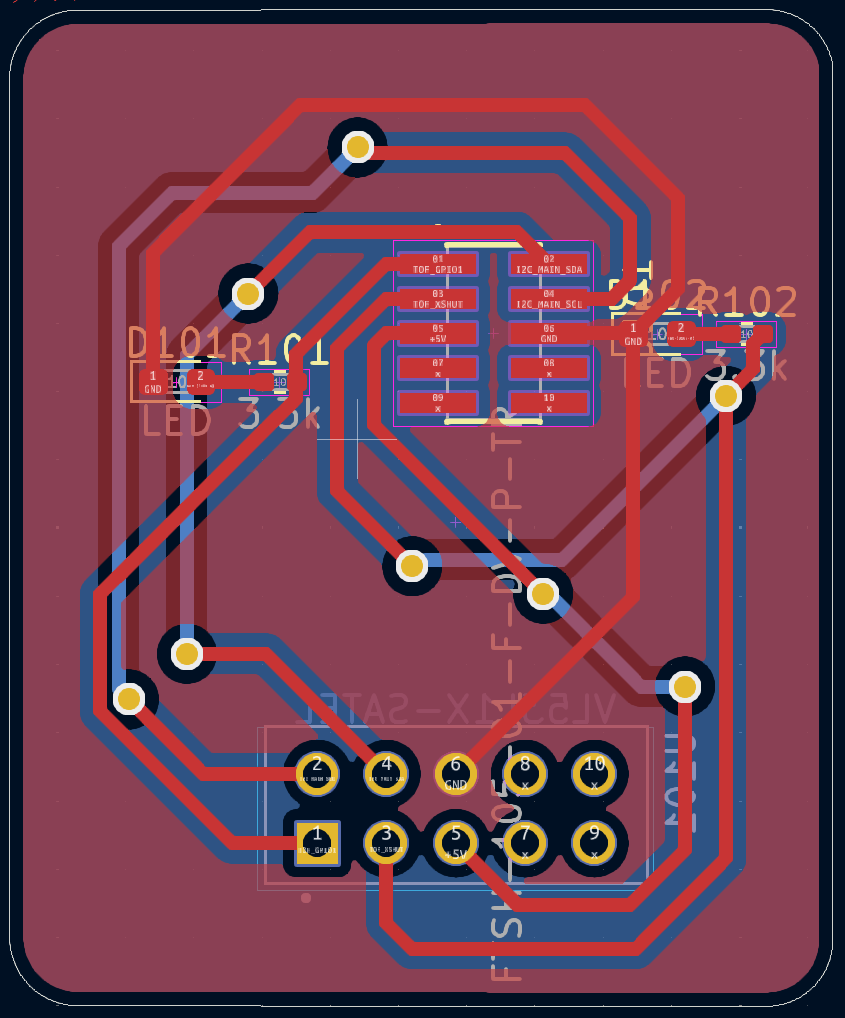
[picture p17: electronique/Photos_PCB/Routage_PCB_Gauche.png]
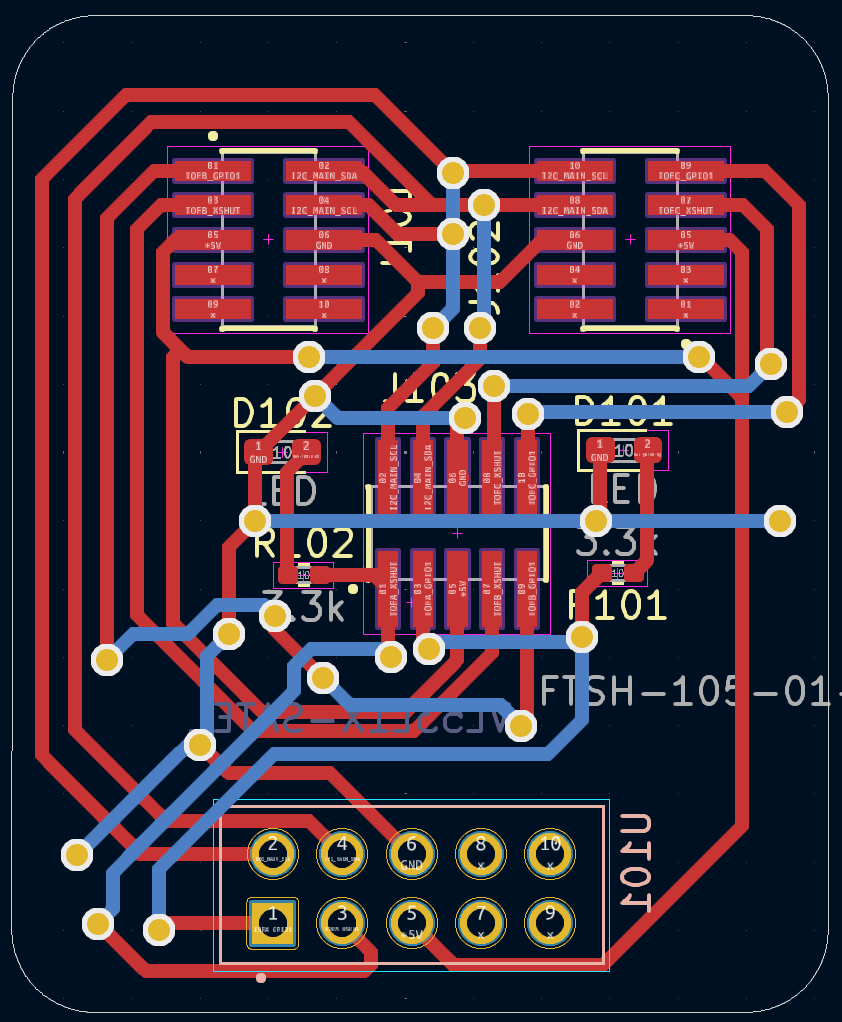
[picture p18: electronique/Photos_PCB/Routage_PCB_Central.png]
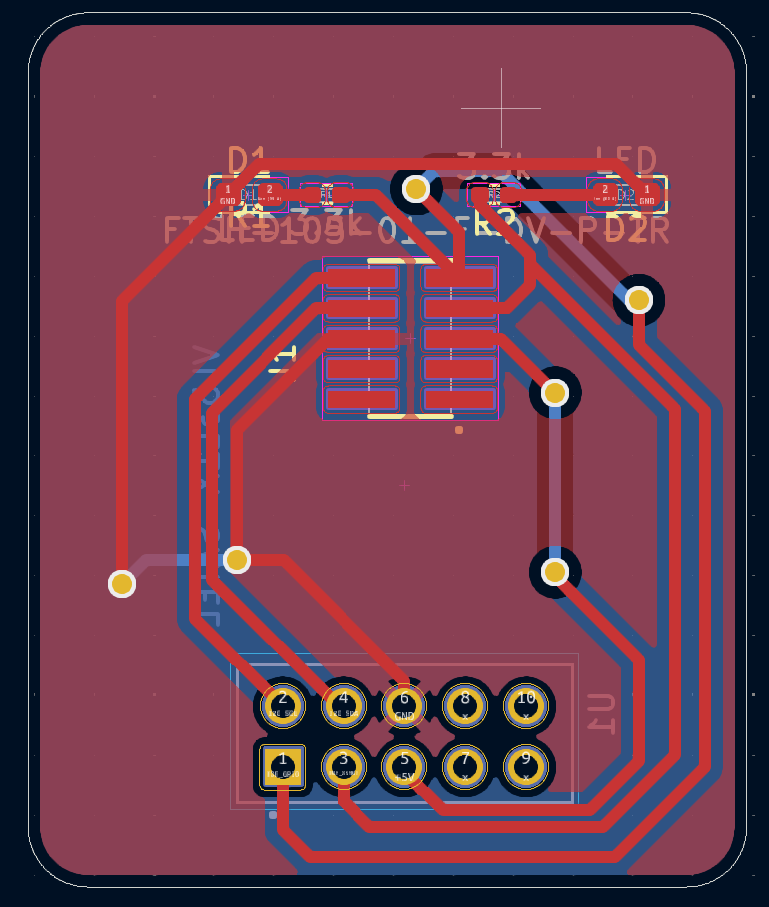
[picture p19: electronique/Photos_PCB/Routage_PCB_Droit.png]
|   |   |  |

Hélas nous n'avons pas utiliser les TOF au final par manque de temps. Nous avons utilisés des capteurs moustaches pour détecter le bord de la table car leur utilisation est beaucoup plus simple que les TOFs.
## Auteurs : 
>* Jolan Thomasset (jolan.thomasset@ensea.fr)  
>* Romain Pace   (romain.pace@ensea.fr)  
>* Rémi Weidle   (remi.weidle@ensea.fr)

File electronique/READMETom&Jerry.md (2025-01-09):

# Partie éléctronique  TOM&JERRY

## Sommaire
- [Présentation](#présentation)
- [Alimentation](#alimentation)
- [Driver Moteurs](#drivers-moteurs)
- [STM32](#stm32)
- [Peripheriques](#périphériques)
- [Peripherique Annexe](#périphériques-annexes)
- [Peripherique Annexe](#périphériques-annexes)
- [Musique](#musique)
- [Routage](#routage)
- [Erreurs](#erreurs-notables)

---

## Présentation
>Bienvenue dans la partie éléctronique du projet, dans ce dossier sont présent tous les fichiers de conception du PCB KiCad ainsi que tous les fichiers de fabrications Gerber.  
Deux fichiers sont actuellement dans le directory. Tom&Jerry_PCB pour le PCB principal et TOF_PCB pour le secondaire.   
Il est détaillé chaque composante du Schématique/PCb principal dans ce ReadMe. Sinon pour les TOF aller [ici](READMETOF.md)

---

## Alimentation
>[!Tip]
>Pour notre robot nous utilisons plusieurs système pour gérer le circuit d'alimentation. On a entre autre un BMS ( Batterie système management ), ainsi qu'un pseudo Power Path Management. La batterie utilisée est la suivante : [here](../datasheet/Batterie.pdf)  

>[!Tip]
>Des connecteurs Pac-Man sont utilisés au niveau de la recharge de batterie afin de pouvoir déconnecter facilement le circuit de charge si il est foireux. De plus un interrupteur est ajouté pour allumer/Eteindre le robot ainsi qu'un fusible pour protéger des surcourants sur la batterie.  

**Recharge de batterie**

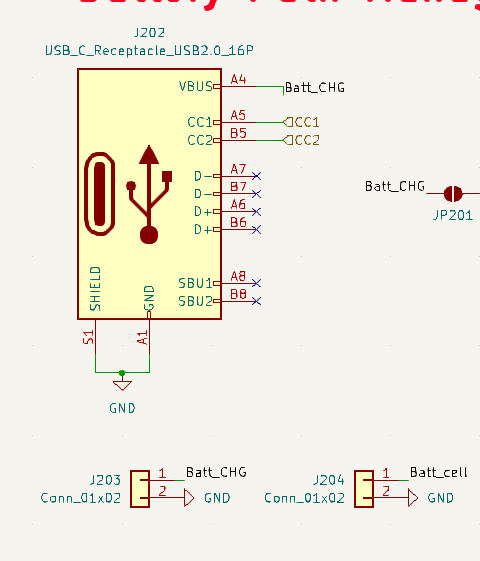
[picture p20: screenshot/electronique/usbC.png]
Recharge


>Pour la recharge de la batterie nous prévoyons deux connecteurs : Type-C et Bornier afin de pouvoir recharger la batterie par alimentation stabilisée de labo ainsi que par cable USB-C (Plus difficile à mettre en oeuvre) [Documentation1](../datasheet/PPM_BMS.pdf).  

Convertisseur linéaire  

>[!Note]
>Cette entrée d'energie est gérée par le **BMS [BQ25172DSGR](../datasheet/BQ25172.pdf) de TI**. Celui-ci est cablé tel quel :  
>* IN : Entrée de tension de charge de batterie. Max 0.8 A (Cf : Doc)  
>* VSET : Programme le nombre de cellule --> 6 cellules + Charge intermittente  
>* ISET : Programme le courant de charge --> 0.8A   
>* TMR : Programme le Timer de sureté --> 6Hr  
>* TS : Programme la température de sureté de charge --> Donnée constructeur    
>* OUT : Sortie de tension de charge de la batterie  
>* STAT : Sortie d'indication de l'état de charge à drain ouvert  
>* EXP : Ground (Pad thermique)  
>* GND : Ground  

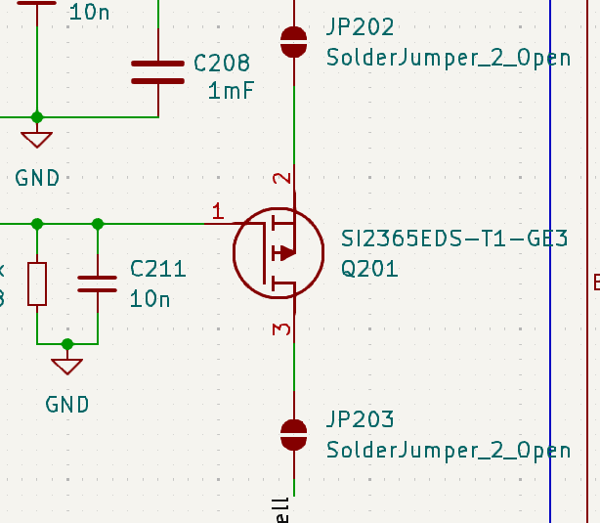
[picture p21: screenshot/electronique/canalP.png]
CanalP


>On a un transistor à canal P pour bloquer la charge du circuit par batterie lorsqu'une tension vient du bornier ou de l'USB-C. De plus on ajoute des condensateur (C...) pour eviter les retours de courant dû a des freinage des roues dans la résistance et donc dans l'alimentation derrière [(Doc)](../datasheet/slua376.pdf).    

Convertisseur linéaire

>[!Important]
>* Actuellement le circuit fonctionne correctement. On a bien le switch entre le circuit de recharge et le circuite de décharge. Rien n'a cramé ce qui est bon signe. 
>* Un petit soucis sur le temps de charge. Il serait mieux d'augmenter le courant possible admissible par la batterie car actuellement celle-ci se recharge en 4h. Cela peut être un peu long. 

>On utilise un premier convertisseur Buck pour abaisser la tension à 5V. Celui-ci est à découpage donc plus cher mais possède un meilleur rendement et un plus faible échauffement. Cela est parfait puisqu'il alimente le lidar ainsi que tous les circuits 3.3v derrière et donc peut avoir des appels de courant assez élevé (Comme démarrage de lidar).  

>[!Note]
>**Convertisseur Buck ([MP1475](../datasheet/MP1475.pdf))**  
>* IN : Tension d'entrée  
>* BST : Bootstrap  
>* SWT : Sortie de commutation  
>* PG : Sortie de puissance  
>* VCC : LDO interne de 5v  
>* EN/SYNC : Pour les clocks externes  
>* FB : Feedback  
>* GND : Ground  

>Actuellement les données sont celle ce la doc. La seule chose réglée est le pont diviseur avec une Vref = 1.25V pour avoir une sortie de 5V en sortie. 

>[!Important]
>* Une erreur a été commise sur l'empreinte de la bobine sur la taille. Il a donc fallu faire une bobine flotante avec deux fils et un ptit coup d'isolant pour éviter les cour-circuits. 

Convertisseur linéaire

>Simple convertisseur linéaire qui abaisse de 5V vers 3.3V pour alimenter certains capteurs ou encore la STM32 qui n'accepte pas du 5V. L'utilisation d'un buck serai plus utile si on recherche la performance cependant un LDO est suffisant car moins couteux, plus simple à mettre en place. L'abaissement de tension est faible sur de faible courants par conséquent la dissipation thermique sera faible ce qui justifie un LDO plutôt qu'un buck.  

>[!Note]
>**Convertisseur LDO [(BU33SD5WG-TR)](../datasheet/buxxsd5wg-e.pdf)**  
>* VIN : Tension d'entrée  
>* GND : Ground  
>* STBY : StandBy --> Ici sur High il marche dés qu'il est alimenté.   
>* N. C. : No Connected pin  
>* Vout : Tension de sortie  

---

## Drivers moteurs
>Afin de pouvoir mouvoir le robot sur la table de jeu, nous utilisons des moteurs type MCC (DfRobot FIT0520). Ces moteurs possèdent des codeurs déjà sur l'arbre moteur ce qui a l'avantage de ne négliger aucun décalage entre une roue de codeur et la roue de l'arbre moteur. Cependant si jamais la roue patine ou glisse le codeur ne prendra pas en compte ce dérapage ce qui entrainera des erreurs. Il faut donc impérativement que la mécanique permette au robot de rester particulièrement stabilisé sur le sol.  

Connecteur Moteur

>[!Note]
>Branché sur la carte les deux moteurs auront de beaux JST-XH de 6 Pins chacun tels que :  
>* Motor - : Phase - du moteur  
>* Motor + : Phase + du moteur  
>* GND : Ground   
>* 5V : Alimentation des codeurs en 5V   
>* Codeur PH1 : Pin allant avec PH2 avec la trame du codeur pour déterminer ensuite la vitesse du robot.   
>* Codeur PH2 : Pin allant avec PH1 avec la trame du codeur pour déterminer ensuite la vitesse du robot.   

>Pour controler ces deux moteurs chaque moteur aura son driver.  

>[!Important]
>* Un petit soucis est à noter sur ces fameux driver mais plus côté STM32. Nous avons pensé qu'un seul timer pouvait controller les encodeurs et les moteurs au lieu de deux timers pour les encodeurs et deux timers pour les moteurs. Par conséquent nous n'avons rien pour utiliser les encodeurs.

Driver Moteur

>[!Note]
>**Driver [ZXBM5210](../datasheet/ZXBM5210.pdf)**  
>* Vref : Tension de référence pour setup l'oscillator PWM du composant.   
>* VDD : Alimentation du composant en 5V   
>* VM : Tension d'alimentation des moteurs  
>* FWD : PWM pour faire avancer le robot  
>* REV : PWM pour faire reculer le robot  
>* Out 1 :  Sortie au moteur phase -  
>* Out 2 : Sortie au moteur phase +  

>[!Important]
>Il est à noter que des capa de découplage sont utilisés afin d'éviter les fluctuation de courant trop rapide sur Vref ( Car tension de référence), sur les phases du moteur afin d'éviter des signaux créneau pur. De plus la documentation suggère un système de diode afin d'éviter la réversibilité du courant vers la batterie. Celui-ci ne sera pas utilisé afin d'éviter de cramer des diodes suite à des quantités trop importantes de courant que se déchargeraient dans les diodes.   

>[!Tip]
>En plus de cela nous utilisons un composant pour mesurer le courant drainé de la batterie vers les moteurs à l'aide d'une résistance dite shunt. Ce composant permettra de nous aider à asservir pourquoi pas en courant mais aussi de protection afin d'éviter comme nous n'avons pas mis les diodes d'avoir des données sur ce qui se passe.  

Mesureur de courant

>[!Note]
>**Mesureur de courant [NCS199A2RSQT2G](../datasheet/NCS199A2RSQT2G.pdf)**  
>* GND : Ground  
>* In + : Entrée + coté résistance de shunt pour capter le courant  
>* In - : Entrée - coté résistance de shunt pour capter le courant  
>* Vs : Tension d'alimentation du composant  
>* Vref : Tension de référence dont je ne sais pas à quoi elle sert (J'ai cable comme la doc)  
>* Out : Sortie du composant avec ke courant prêt à être lu par un ADC  

>Comme toute entrée de composant celui-ci ne fait pas l'impasse une capacité de découplage a été ajoutée. De plus la résistance de 1kOhm a été mise pour préparer l'entrée du courant dans l'ADC conforme à la documentation.  

---

## STM32 
>[!Important]
>Avant de développer sur la STM32 et la facon dont nous avons répartis les pins de celle-ci. Pour que celle-ci fonctionne correctement nous utiliserons un quartz externe pour cadencer la STM32 (Configuré dans l'IOC de STM32CubeIDE). 

GPIO Extender

>[!Important]
>De plus nous utilisons une connexion STLink pour le debug de la carte via PC. 

STLink

---

## Périphériques 

>[!Note]
>La carte actuelle va gérer certains capteurs. Avec ceux-ci le robot pourra (Nous l'esperons --> ca ne sert plus à rien d'esprer nous n'avons plus d'encodeur esperer sert a rien.) se repérer sur la table et réaliser au mieux la stratégie mise en place. 

>[!Tip]
> Afin de détecter les bords nous avons décider de faire de la redondance. En effet nous utilisons des capteurs "Moustache" ainsi que TOF pour repérer les bords de la table et éviter que les robots tombent. L'avantage des capteurs moustache est qu'ils sont mécanique donc fiable maintenant cela demande de na pas louper son intégration sur la base roulante ce qui n'es tpas gagner. Pour cela nous pouvvons utiliser les TOF. Ceux-ci sont plus simple à positionner sur le robot et à fonctionner. Cependant l'exploitation des données est plus dure (I2C + GPIO Extender...). 

Moustache

>[!Note]
>Branché sur la carte les quatre capteurs moustahce ont un JST  :  
>* 3.3V : Alimentation
>* GND : Ground  
>Ceux-ci marchent en interrupteur pas besoin de plus de chose pour lire leurs données. 

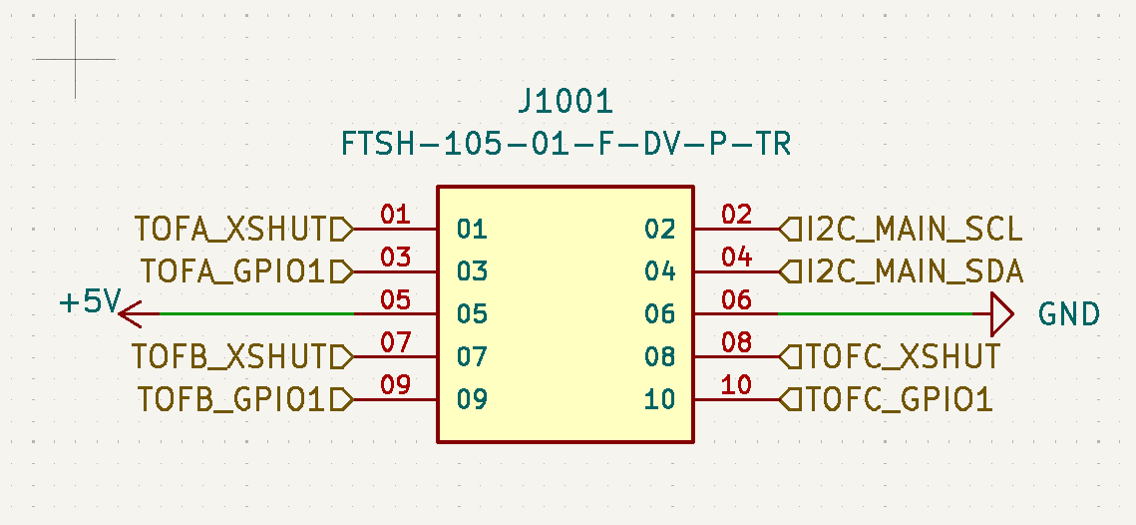
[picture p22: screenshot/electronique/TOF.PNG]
TOF


>[!Note]
>**Capteurs TOF [VL53L1X](../datasheet/VL53L1X.pdf):**   
>* AVDDVCSEL : VCSEL tension d'alimentation  
>* AVSSVCSEL : VCSEL Ground    
>* GND1 - GND4 : Ground  
>* XShut: Pin pour shutdown le composant. celui-ci est actif sur un signal Bas  
>* GPIO1 : GPIO pour gérer les interruptions  
>* DNC : A ne pas connecter (Doit être floating)  
>* SDA : Serial data bus
>* SCL : Serial clock bus
>* AVDD : Tension d'alim du composant
>Ceux-ci sont sur les cartes fournient avec produit par STM32. 

>[!Important]
>* Les capteurs TOF n'ont pas été réalisés par manque de temps et de test. Il fallait utiliser le GPIO expander en plus mais avec tout ce que nous avions à sortir nous avons abandonné cette partie mais elle devrait fonctionner (Théoriquement par un étudiant ce qui est suffisant pour y re-réfléchir). 
>* Pour la suite les bords ne seront détéctés uniquement par des capteurs de fin de course pour faire les demi-tours et donc repartir sans tomber. 

>[!Note]
>En plus de la détection de bord avec les TOF et les capteurs "Moustache", le robot aura un IMU pour faire de la fusion de donnée (Rédigé en septembre ca ne sera pas traité pas assez de temps --> Confirmé la veille de la date limite a 00H05) ainsi que de vérifier si un robot nous touche. De plus il y aura un lidar pour détecter les robots sur la table et foncer sur eux. 

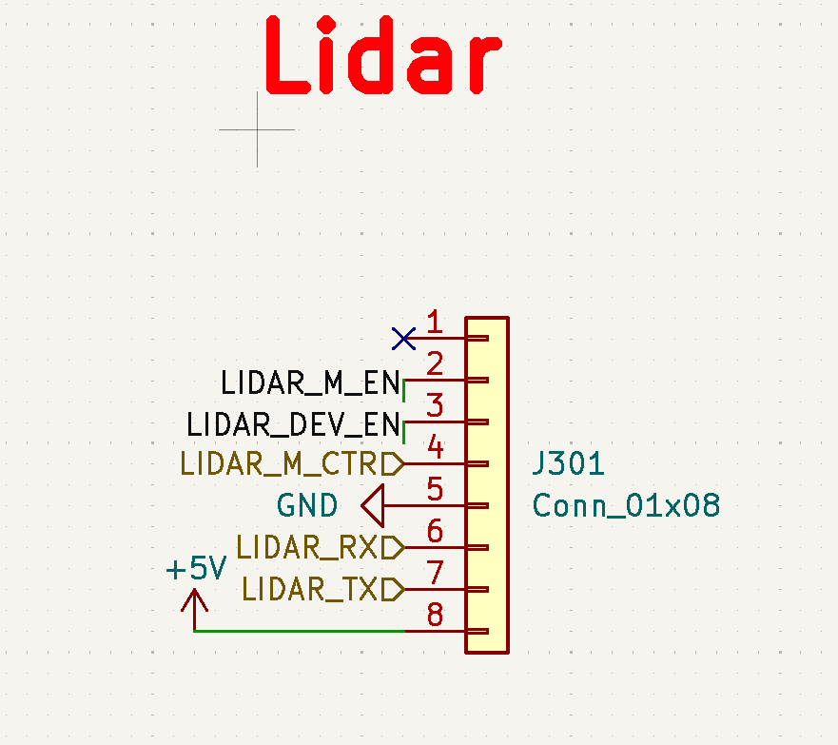
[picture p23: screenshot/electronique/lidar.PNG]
Lidar


>[!Note]
>**Capteurs TOF [YDLidar X2](../datasheet/YdLidarX4.pdf):**   
>* NC : Non connected pin   
>* TX : Sortie UART avec les données du LIDAR   
>* RX : Entrée UART avec les données du LIDAR   
>* GND : Ground    
>* M_EN Motor enable control   
>* DEV_EN Ranging enable control  
>* M_CTR : Entrée de la PWM du moteur du Lidar      
>* VCC Power supply  

>* VCC : Tension d'alimentation du lidar (5v)  

 IMU

>[!Note]
>**IMU [ADXL343](../datasheet/ADXL343.pdf):**   
>* Vs : Tension d'alimentation du composant   
>* GND : Ground   
>* VDD : Tension d'alimentation de l'interface digitale  
>* SDA : Serial data bus  
>* SCL : Serial clock bus  
>* SDO : I2C adresse  
>* NC : A garder non connecte  
>* Int1 - Int2 : Pin d'interruption   
>* CS : Chip Select

---

## Périphériques Annexes 
>Deux composants non imposés ont été utilisés en plus de ceux imposés afin de pouvoir tout connecter à la STM32. Suite à la solution technique des TOF employé le nombre de GPIO recquis a quelque peu explosé surpassant la capacité de la STM. par conséquent un GPIO Extender est utilisé pour ajouter des GPIO afin de couper et utiliser les TOF lorsque nous en avons besoin.   

GPIO Extender

>[!Note]
>**GPIO Extender [TCA9555RTWR](../datasheet/TCA9555.pdf)**  
>* A0 : Adress Input 0  
>* A1 : Adress Input 1  
>* A2 : Adress Input 2  
>* GND : Ground   
>* P00 à P17 : P/port I/O connecte comme Input au démarrage.   
>* SCL : Serial clock bus  
>* SDA : Serial data bus  
>* VCC : Tension d'alimentation du composant  
>* INT : Permet de donner des interruptions avec une Pull-Up resistance.   

>[!Tip]
>En plus de ce composant nous avons utilisé un petit composant pour traiter nos leds. En effet en comptant 4 de débugs, robot allumé, chat/souris,... Nous nous sommes sentis à l'étroit et avons décidé de rajouter un composant qui drive 4 RGB. Cela sera parfait pour débug et montrer les informations nécessaires.  

RGB Led Driver

>[!Note]
>**RGB LED Driver [LP5812CDSDR](../datasheet/LP5812.pdf)**  
>* VCC : Tension d'alimentation du composant  
>* GND : Ground  
>* SYNC : Synchro du composant sur GND (C'est la doc je sais pas pk)  
>* SCL : Serial clock bus  
>* SDA : Serial data bus   
>* OUT0 - OUT3 : Sorties vers les LED   

>Pour ce composant nous verrons pour le faire marcher en temps voulu avec le SPI pour allumer nos LEDS. Celles-ci sont cablés comme décrit dans la documentation.   

---

## Musique 
>Ayant dans notre groupe notre jolan nationnal, le projet ne pouvait être correctement réalisé sans l'ajout de bout de musique sur le robot. Pour se faire les sorties DAC de la STM32 dédiées seront utilisées. Ce signal audio sera amplifié par un amplificateur de Classe D puis va être envoyé dans des hauts parleurs.   

Musique

>[!Note]
>**Ampli de Classe D [PAM8302AAY](../datasheet/PAM8302A.pdf)**  
>* IN + : Entrée DAC  +  
>* IN - : Entrée DAC  -   
>* SD : Doit rester sur HIGh pour éviter qu'il soit shutdown (donc relié à 3.3v)  
>* VDD : Alimentation du composant  
>* OUT + : Sortie + du haut parleur   
>* OUT - : Sortie - du haut parleur  

>[!Important]
>Les deux capacité de découplage ainsi que les deux ferrites sont celles conforme à la documentation afin de réduire les interférence electromagnétique à partir de 1MHz et au dela. Ceci est parfait puisque ce composant est à coté de composant sensible comme la STM...  

## Routage 
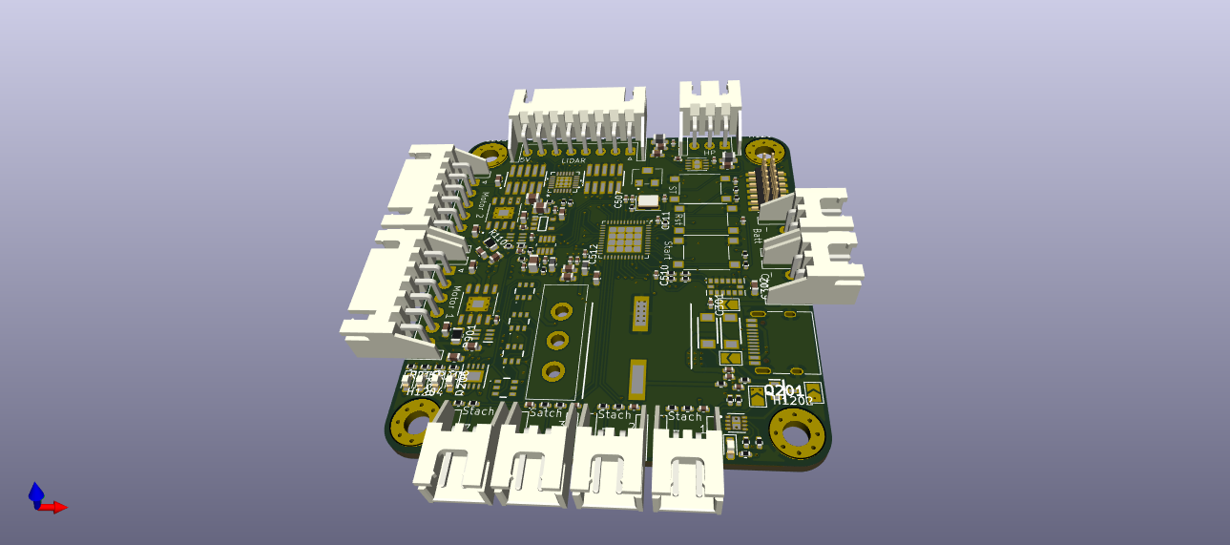
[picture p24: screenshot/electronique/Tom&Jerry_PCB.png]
PCB


> Le PCB a été particulièrement difficile à router. Beaucoup de composants devaient être placées en peu d'espace. Certaines contraintes physique ont cependant dû être vérifiée afin que le montage se passe au mieux. Les condensateurs de découplage de la SMT32 ont été placé au plus proche de celle-ci afin d'éviter les reboot intempestif. De plus le crystal a été placé au plus proche aussi. Enfin les connecteurs sortent des dimensions avec un silkscreen entièrement remanié à cause de la superposition du nom des composants. 

## Erreurs notables 

>[!Important] 
>* Il faut vérifier absolument ces points qui ont été mal réalisé auparavant.   
>* L'empreinte de la bobine pour l'entrée ADC doit avoir la bonne empreinte. Le cas échéant ceci peut amener à des soucis notables.   
>* Une erreur a été commise sur l'attribution des timer en effet les encodeur prennent un advance timer chacun pour obtenir la vitesse du robot. Or nous en avons mis deux sur le même timer. Pour la suite du projet nous n'avons pas pu réaliser la partie encoder. Il suffirait de déplacer un encoder sur un autre timer  compatible avec le mode encoder.   
>* Un petit via a été oublié sur le driver d'un moteur empechant celui-ci de fonctionner correctement. 
>* On a alimenté le GPIO Expander en 5v ce qui fait des sorties d'état haut du GPIO expander à 5v. Ce qui est trop élevé pour le lidar heureusement on asservit pas sa vitesse de rotation en prenant celle de base. De plus les tof supportent cette tension d'état aux états haut (Ca reste pas un soucis car on s'en sert pas). --> Solution alimenter le gpio expander en 3.3v ...

>[!Important] 
>* **Il est important de noter que touts ces soucis ont été corrigé dans le commit :**

## Auteurs : 
>* Jolan Thomasset (jolan.thomasset@ensea.fr)  
>* Romain Pace   (romain.pace@ensea.fr)  
>* Rémi Weidle   (remi.weidle@ensea.fr)

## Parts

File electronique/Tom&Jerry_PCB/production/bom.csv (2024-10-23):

Designator | Footprint | Quantity | Value | LCSC Part #
C1, C2 | 0603 | 2 | 10uF
C1101, C401, C507, C901 | 0402 | 4 | 100nF
C1102, C1103, C1104, C902, C903, C904 | 0603 | 6 | 1uF
C1301, C1501, C1601, C1701, C207, C211, C502, C506, C508, C509 | 0402 | 10 | 10n
C201, C203, C204 | 0805 | 3 | 22uF
C202 | 0402 | 1 | 0.1u
C205, C209 | 0402 | 2 | 0.1uF
C206, C301, C510, C511, C512, C605 | 0402 | 6 | 100n
C208 | CAPAE1350X1400N | 1 | 1mF
C210 | 0402 | 1 | 15pF
C212, C213, C503, C505, C602, C604 | 0603 | 6 | 1u
C302 | 0603 | 1 | 0.1u
C501, C504 | 0402 | 2 | 10p
C513 | 0603 | 1 | 4.7u
C601 | 0603 | 1 | 10u
C603, C606 | 0402 | 2 | 220p
D201, D202 | SODFL4825X110N | 2 | D
D203, D204, D205, D206, D207 | 0603 | 5 | LED
FB601, FB602 | 0805 | 2 | FerriteBead_Small
IC1101, IC901 | SOT65P210X110-6N | 2 | NCS199A2RSQT2G
IC301 | RTW24_2P45X2P45 | 1 | TCA9555RTWR
J1001, J701 | SAMTEC_FTSH-105-01-F-DV-P-TR | 2 | FTSH-105-01-F-DV-P-TR
J1301, J1501, J1601, J1701, J203, J204 | JST_XH_S2B-XH-A-1_1x02_P2.50mm_Horizontal | 6 | Conn_01x02
J201 | Switch-3 | 1 | Interrupteur
J202 | USB_C_Receptacle_HRO_TYPE-C-31-M-12 | 1 | USB_C_Receptacle_USB2.0_16P
J301 | JST_XH_S8B-XH-A_1x08_P2.50mm_Horizontal | 1 | Conn_01x08
J401, J402 | JST_XH_S6B-XH-A_1x06_P2.50mm_Horizontal | 2 | Conn_01x06
J501 | PinHeader_2x07_P1.27mm_Vertical_SMD | 1 | Conn_ST_STDC14
J601 | JST_XH_S3B-XH-A_1x03_P2.50mm_Horizontal | 1 | Conn_01x03
L201 | 0603 | 1 | 4.7uH
L501 | 0603 | 1 | 39n
LED801, LED802, LED803, LED804 | 5988G10313F | 4 | RGB
PS201 | SOT95P280X125-5N | 1 | BU33SD5WG-TR
Q201 | SOT95P237X112-3N | 1 | SI2365EDS-T1-GE3
R101, R102, R103, R104, R1301, R1302, R1501, R1502, R1601, R1602, R1701, R1702, R213, R503, R504, R505, R506 | 0402 | 17 | 10k
R1101, R901 | 0805 | 2 | 0.015
R201 | 0402 | 1 | 20
R202 | 0402 | 1 | 100m
R203, R204, R401, R402, R502 | 0402 | 5 | 100k
R205 | 0402 | 1 | 16k
R206 | 0402 | 1 | 40.2k
R207 | 0402 | 1 | 7.68k
R208 | 0402 | 1 | 15k
R209, R214, R215, R216, R217 | 0402 | 5 | 3.3k
R210 | 0402 | 1 | 3.6k
R211, R212 | 0402 | 2 | 27k
R501 | 0402 | 1 | 10R
RV601 | Potar | 1 | R_Potentiometer
SW501, SW502, SW503 | SW_Push_1P1T_NO_6x6mm_H9.5mm | 3 | SW_Push
U1101, U901 | XBM5210 | 2 | ZXBM5210-S
U201 | SOT65P280X100-8N | 1 | MP1475DJ-LF-P
U202 | IC_BQ25172DSGR | 1 | BQ25172DSGR
U301 | PQFN80P300X500X100-14N | 1 | ADXL343
U501 | QFN-48-1EP_7x7mm_P0.5mm_EP5.1x5.1mm | 1 | STM32G431CBU6
U601 | DFN300X300X80-8N | 1 | PAM8302AAY
U801 | WSON8_DSD_TEX | 1 | LP5812ADSDR
Y501 | Crystal_SMD_EuroQuartz_MT-4Pin_3.2x2.5mm | 1 | 16MHz

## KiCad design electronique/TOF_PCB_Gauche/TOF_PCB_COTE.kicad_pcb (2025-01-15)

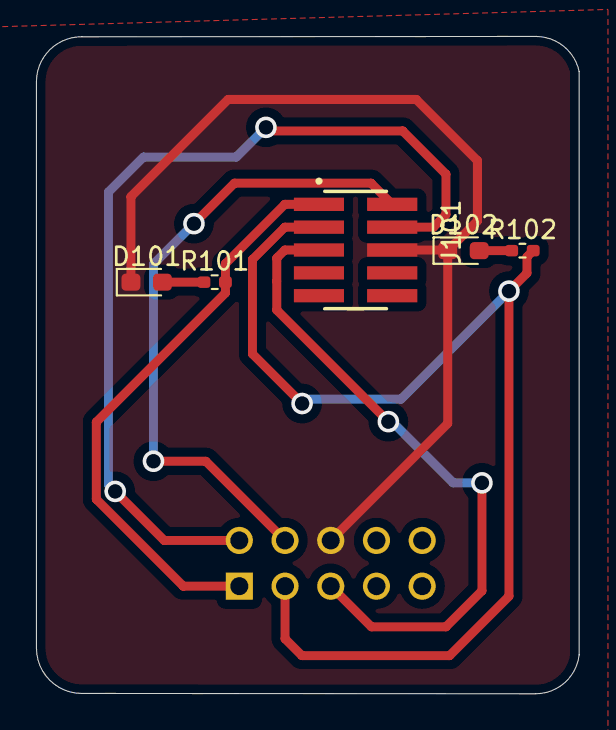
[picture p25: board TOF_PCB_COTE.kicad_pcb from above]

Board: 2 copper layers, 30.2 x 36.5 mm, 6 parts (1 on the bottom side), 8 nets.

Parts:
D101, D102: LED; LED_0603_1608Metric_Pad1.05x0.95mm_HandSolder
J101: FTSH-105-01-F-DV-P-TR; SAMTEC_FTSH-105-01-F-DV-P-TR
R101, R102: 3.3k; R_0402_1005Metric_Pad0.72x0.64mm_HandSolder
U101: VL53L1X-SATEL; MODULE_VL53L1X-SATEL

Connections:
+5V: J101.05, U101.5 (VDD)
/I2C_MAIN_SCL: J101.04, U101.2 (SCL_I)
/I2C_MAIN_SDA: J101.02, U101.4 (SDA_I)
/TOF_GPIO1: J101.01, R101.2, U101.1 (INT_I)
/TOF_XSHUT: J101.03, R102.2, U101.3 (XSDN_I)
GND: D101.1 (K), D102.1 (K), J101.06, U101.6 (GND)
unnamed: D101.2 (A), R101.1
unnamed: D102.2 (A), R102.1

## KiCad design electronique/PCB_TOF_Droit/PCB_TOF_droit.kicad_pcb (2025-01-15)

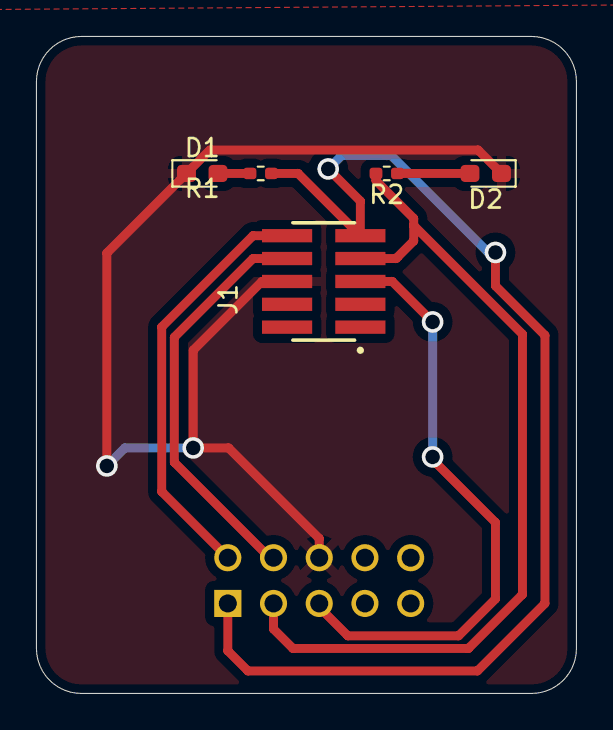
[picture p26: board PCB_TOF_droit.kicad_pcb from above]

Board: 2 copper layers, 30.0 x 36.5 mm, 6 parts (1 on the bottom side), 8 nets.

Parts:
D1, D2: LED; LED_0603_1608Metric_Pad1.05x0.95mm_HandSolder
J1: FTSH-105-01-F-DV-P-TR; SAMTEC_FTSH-105-01-F-DV-P-TR
R1, R2: 3.3k; R_0402_1005Metric_Pad0.72x0.64mm_HandSolder
U1: VL53L1X-SATEL; MODULE_VL53L1X-SATEL

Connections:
+5V: J1.05, U1.5 (VDD)
/I2C_SCL: J1.10, U1.2 (SCL_I)
/I2C_SDA: J1.08, U1.4 (SDA_I)
/TOF_GPIO: J1.09, R1.2, U1.1 (INT_I)
/TOF_XSHUT: J1.07, R2.2, U1.3 (XSDN_I)
GND: D1.1 (K), D2.1 (K), J1.06, U1.6 (GND)
unnamed: D1.2 (A), R1.1
unnamed: D2.2 (A), R2.1

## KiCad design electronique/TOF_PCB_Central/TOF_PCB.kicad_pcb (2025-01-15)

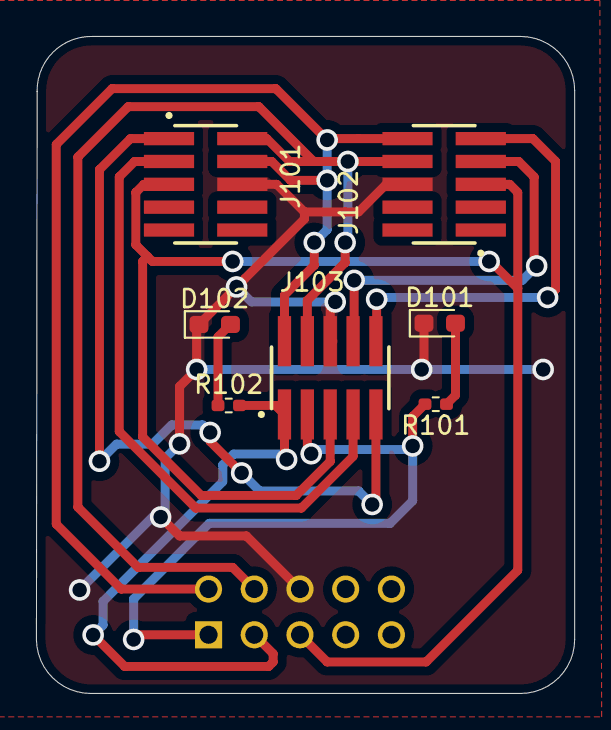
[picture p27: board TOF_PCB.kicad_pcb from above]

Board: 2 copper layers, 29.9 x 36.5 mm, 8 parts (1 on the bottom side), 12 nets.

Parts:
D101, D102: LED; LED_0603_1608Metric_Pad1.05x0.95mm_HandSolder
J101, J102, J103: FTSH-105-01-F-DV-P-TR; SAMTEC_FTSH-105-01-F-DV-P-TR
R101, R102: 3.3k; R_0402_1005Metric_Pad0.72x0.64mm_HandSolder
U101: VL53L1X-SATEL; MODULE_VL53L1X-SATEL

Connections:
+5V: J101.05, J102.05, J103.05, U101.5 (VDD)
/I2C_MAIN_SCL: J101.04, J102.10, J103.02, U101.2 (SCL_I)
/I2C_MAIN_SDA: J101.02, J102.08, J103.04, U101.4 (SDA_I)
/TOFA_GPIO1: J103.03, R101.2, U101.1 (INT_I)
/TOFA_XSHUT: J103.01, R102.2, U101.3 (XSDN_I)
/TOFB_GPIO1: J101.01, J103.09
/TOFB_XSHUT: J101.03, J103.07
/TOFC_GPIO1: J102.09, J103.10
/TOFC_XSHUT: J102.07, J103.08
GND: D101.1 (K), D102.1 (K), J101.06, J102.06, J103.06, U101.6 (GND)
unnamed: D101.2 (A), R101.1
unnamed: D102.2 (A), R102.1

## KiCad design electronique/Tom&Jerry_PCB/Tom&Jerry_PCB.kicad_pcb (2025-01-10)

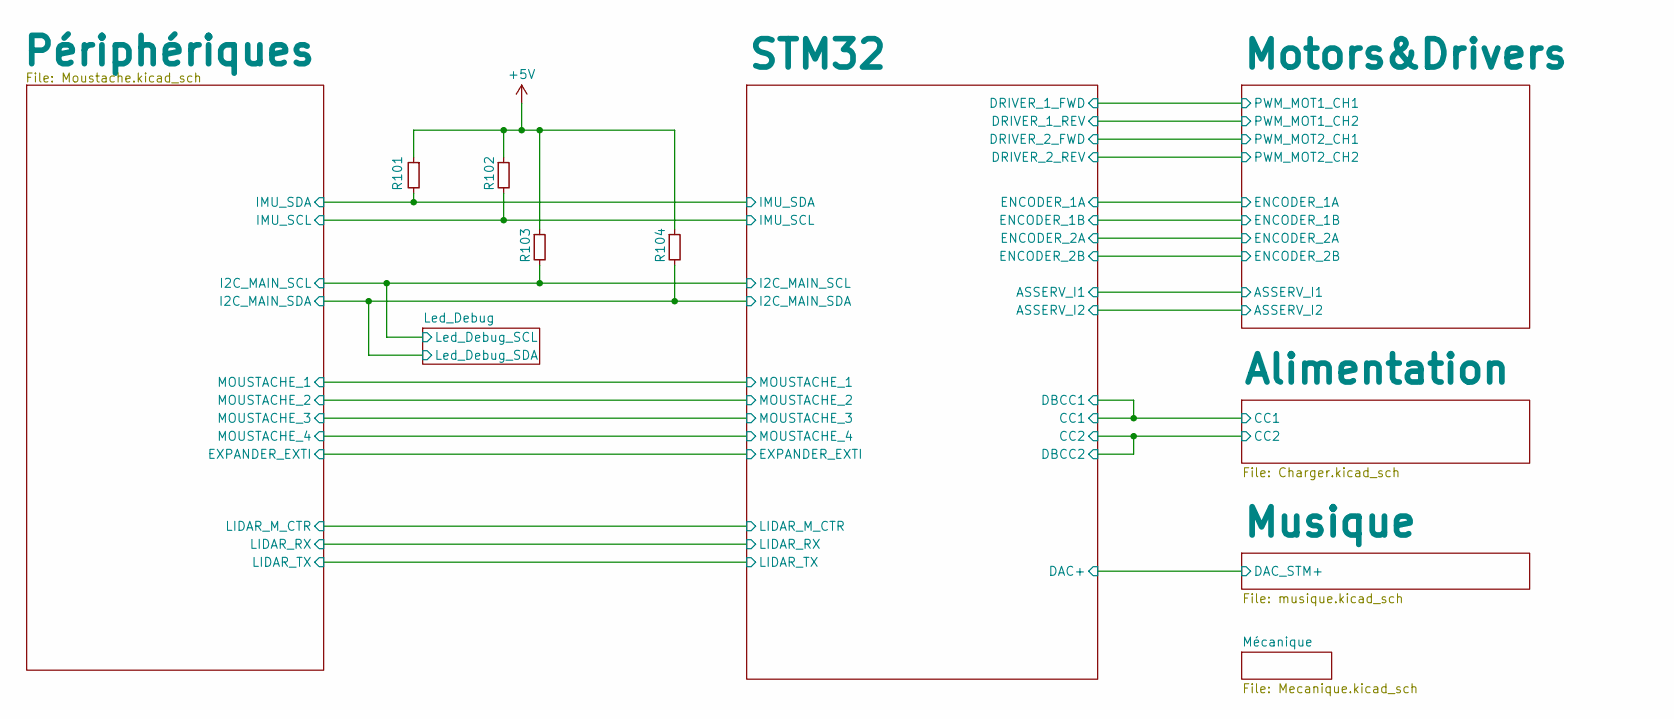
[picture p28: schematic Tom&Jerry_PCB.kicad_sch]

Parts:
R101, R102, R103, R104: 10k; R_0402_1005Metric

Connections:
+5V: R101.1, R102.1, R103.1, R104.1; also elsewhere on the board
/Led_Debug/Led_Debug_SCL: R103.2; also elsewhere on the board
/Led_Debug/Led_Debug_SDA: R104.2; also elsewhere on the board
/Périphériques/IMU_SCL: R102.2; also elsewhere on the board
/Périphériques/IMU_SDA: R101.2; also elsewhere on the board

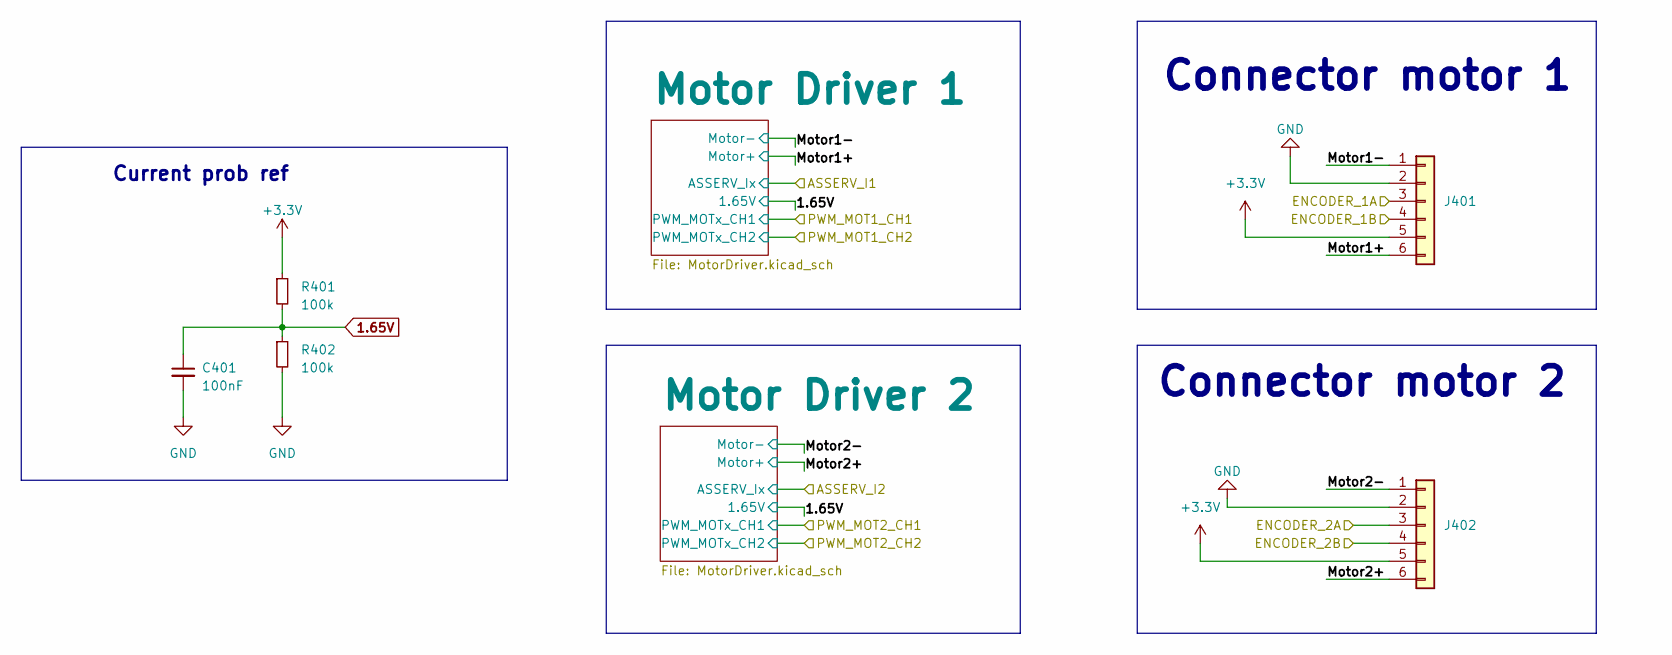
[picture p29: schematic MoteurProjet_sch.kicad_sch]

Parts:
C401: 100nF; C_0402_1005Metric
J401, J402: Conn_01x06; JST_XH_S6B-XH-A_1x06_P2.50mm_Horizontal
R401, R402: 100k; R_0402_1005Metric

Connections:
1.65V: C401.1, R401.2, R402.1; also elsewhere on the board
+3.3V: J401.5, J402.5, R401.1; also elsewhere on the board
/Motors&Drivers/ENCODER_1A: J401.3; also elsewhere on the board
/Motors&Drivers/ENCODER_1B: J401.4; also elsewhere on the board
/Motors&Drivers/ENCODER_2A: J402.3; also elsewhere on the board
/Motors&Drivers/ENCODER_2B: J402.4; also elsewhere on the board
/Motors&Drivers/Motor1+: J401.6; also elsewhere on the board
/Motors&Drivers/Motor1-: J401.1; also elsewhere on the board
/Motors&Drivers/Motor2+: J402.6; also elsewhere on the board
/Motors&Drivers/Motor2-: J402.1; also elsewhere on the board
GND: C401.2, J401.2, J402.2, R402.2; also elsewhere on the board

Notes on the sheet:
Current prob ref
Connector motor 1
Connector motor 2

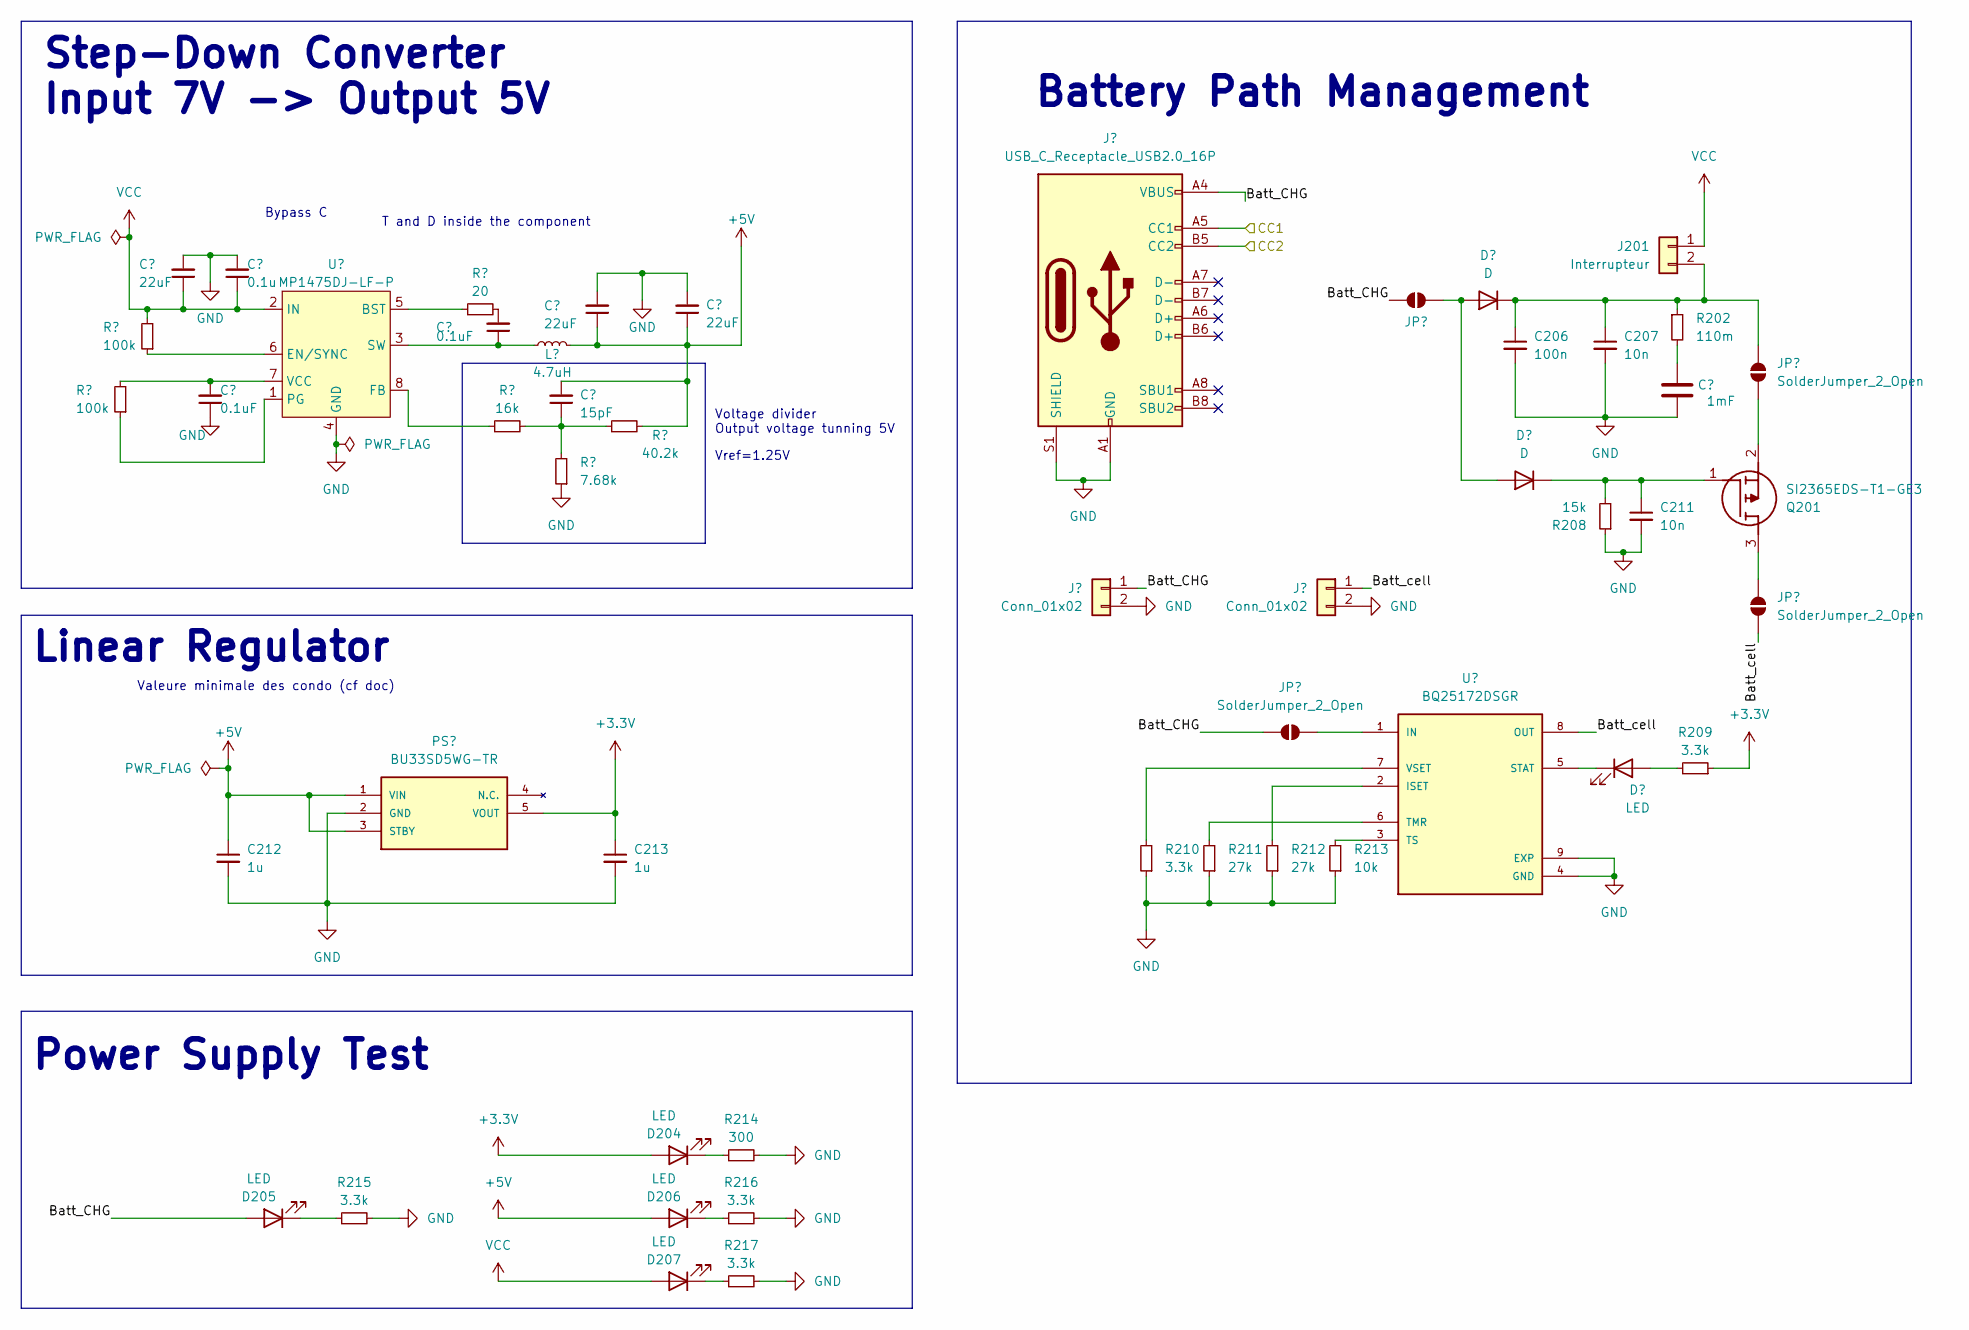
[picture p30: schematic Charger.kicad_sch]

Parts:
C201, C203, C204: 22uF; C_0805_2012Metric
C202: 0.1u; C_0402_1005Metric
C205, C209: 0.1uF; C_0402_1005Metric
C206: 100n; C_0402_1005Metric
C207, C211: 10n; C_0402_1005Metric
C208: 1mF; CAPAE1350X1400N
C210: 15pF; C_0402_1005Metric
C212, C213: 1u; C_0603_1608Metric
D201, D202: D; SODFL4825X110N
D203, D204, D205, D206, D207: LED; LED_0603_1608Metric_Pad1.05x0.95mm_HandSolder
J201: Interrupteur; Switch-3
J202: USB_C_Receptacle_USB2.0_16P; USB_C_Receptacle_HRO_TYPE-C-31-M-12
J203, J204: Conn_01x02; JST_XH_S2B-XH-A-1_1x02_P2.50mm_Horizontal
JP201, JP202, JP203, JP204: SolderJumper_2_Open; SolderJumper-2_P1.3mm_Open_TrianglePad1.0x1.5mm
L201: 4.7uH; L_0603_1608Metric_Pad1.05x0.95mm_HandSolder; Manufacturer_Part_Number 74438356047HT; Mouser Part Number 710-74438356047HT
PS201: BU33SD5WG-TR; SOT95P280X125-5N; Mouser_Part_Number 755-BU33SD5WG-TR
Q201: SI2365EDS-T1-GE3; SOT95P237X112-3N; Mouser Part Number 78-SI2365EDS-T1-GE3
R201: 20; R_0402_1005Metric
R202: 110m; R_0402_1005Metric
R203, R204: 100k; R_0402_1005Metric
R205: 16k; R_0402_1005Metric
R206: 40.2k; R_0402_1005Metric
R207: 7.68k; R_0402_1005Metric
R208: 15k; R_0402_1005Metric
R209, R210, R215, R216, R217: 3.3k; R_0402_1005Metric
R211, R212: 27k; R_0402_1005Metric
R213: 10k; R_0402_1005Metric
R214: 300; R_0402_1005Metric
U201: MP1475DJ-LF-P; SOT65P280X100-8N; Manufacturer_Part_Number MP1475DJ; Mouser Part Number 946-MP1475DJLFP
U202: BQ25172DSGR; IC_BQ25172DSGR; PARTREV June 2022

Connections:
+3.3V: C213.1, D204.2 (A), PS201.5 (VOUT), R209.1; also elsewhere on the board
+5V: C203.1, C204.1, C210.2, C212.1, D206.2 (A), L201.1, PS201.1 (VIN), PS201.3 (STBY), R206.2; also elsewhere on the board
/Alimentation/Batt_CHG: D205.2 (A), J202.A4 (VBUS), J202.A9 (VBUS), J202.B4 (VBUS), J202.B9 (VBUS), J203.1, JP201.1 (A), JP204.2 (B)
/Alimentation/Batt_cell: J204.1, JP203.1 (A), U202.8 (OUT)
/Alimentation/CC1: J202.A5 (CC1); also elsewhere on the board
/Alimentation/CC2: J202.B5 (CC2); also elsewhere on the board
GND: C201.2, C202.2, C203.2, C204.2, C206.2, C207.2, C208.2, C209.1, C211.2, C212.2, C213.2, J202.A1 (GND), J202.A12 (GND), J202.B1 (GND), J202.B12 (GND), J202.S1 (SHIELD), J203.2, J204.2, PS201.2 (GND), R207.1, R208.1, R210.1, R211.1, R212.1, R213.1, R214.2, R215.2, R216.2, R217.2, U201.4 (GND), U202.4 (GND), U202.9 (EXP); also elsewhere on the board
unnamed: C205.2, R201.2
unnamed: C208.1, R202.2
unnamed: C210.1, R205.2, R206.1, R207.2
unnamed: D201.2 (A), D202.2 (A), JP201.2 (B)
unnamed: C206.1, C207.1, D201.1 (K), J201.2, JP202.2 (B), R202.1
unnamed: C211.1, D202.1 (K), Q201.1 (G), R208.2
unnamed: D203.2 (A), R209.2
unnamed: D203.1 (K), U202.5 (STAT)
unnamed: D204.1 (K), R214.1
unnamed: D205.1 (K), R215.1
unnamed: D206.1 (K), R216.1
unnamed: D207.1 (K), R217.1
unnamed: JP202.1 (A), Q201.2 (S)
unnamed: JP203.2 (B), Q201.3 (D)
unnamed: JP204.1 (A), U202.1 (IN)
unnamed: R201.1, U201.5 (BST)
unnamed: R203.1, U201.6 (EN/SYNC)
unnamed: R205.1, U201.8 (FB)
unnamed: R204.1, U201.1 (PG)
unnamed: C205.1, L201.2, U201.3 (SW)
unnamed: C209.2, R204.2, U201.7 (VCC)
unnamed: R212.2, U202.2 (ISET)
unnamed: R211.2, U202.6 (TMR)
unnamed: R213.2, U202.3 (TS)
unnamed: R210.2, U202.7 (VSET)
VCC: C201.1, C202.1, D207.2 (A), J201.1, R203.2, U201.2 (IN); also elsewhere on the board

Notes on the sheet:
T and D inside the component
Valeure minimale des condo (cf doc)
Voltage divider Output voltage tunning 5V
Linear Regulator
Vref=1.25V
Step-Down Converter Input 7V -> Output 5V
Battery Path Management
Bypass C
Power Supply Test

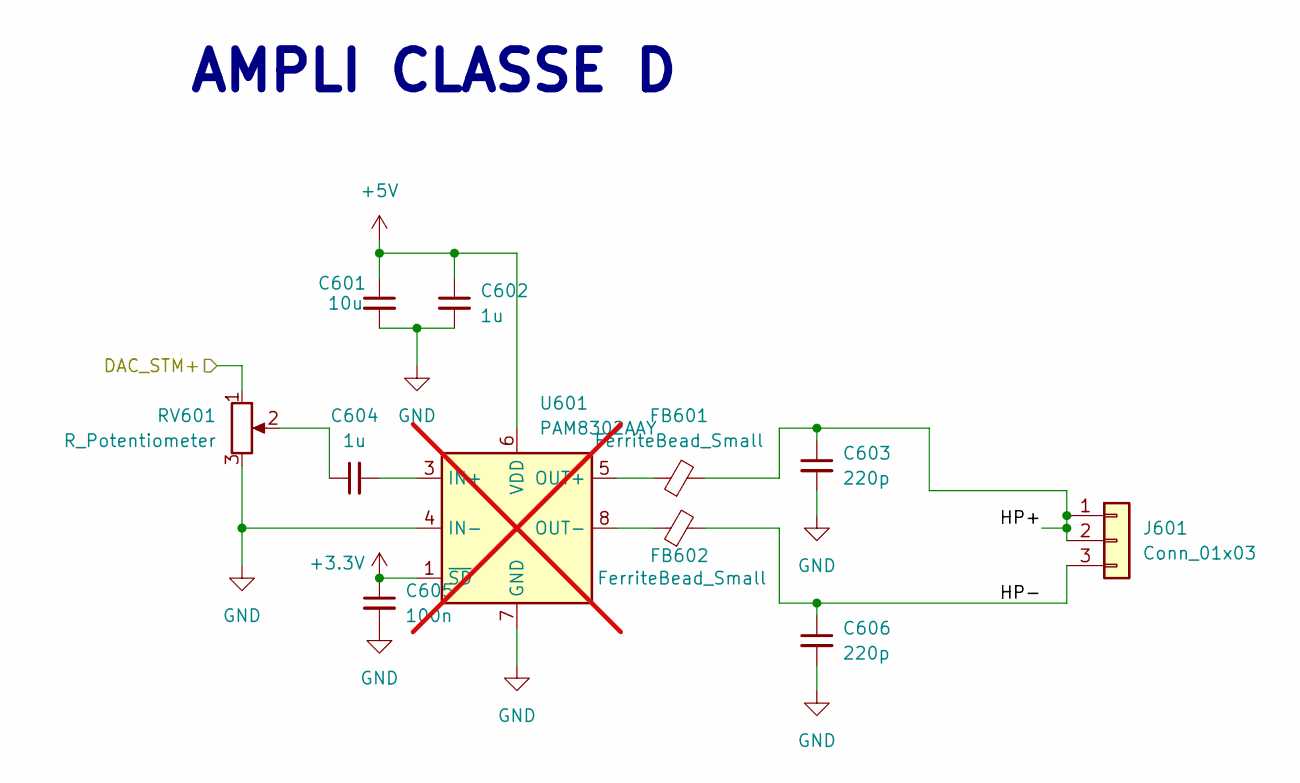
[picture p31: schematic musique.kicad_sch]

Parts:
C601: 10u; C_0603_1608Metric
C602, C604: 1u; C_0603_1608Metric
C603, C606: 220p; C_0402_1005Metric
C605: 100n; C_0402_1005Metric
FB601, FB602: FerriteBead_Small; L_0805_2012Metric
J601: Conn_01x03; JST_XH_S3B-XH-A_1x03_P2.50mm_Horizontal
RV601: R_Potentiometer; Potar
U601: PAM8302AAY; DFN300X300X80-8N; not fitted

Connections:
+3.3V: C605.1, U601.1 (~SD); also elsewhere on the board
+5V: C601.1, C602.1, U601.6 (VDD); also elsewhere on the board
/Musique/DAC_STM+: RV601.1; also elsewhere on the board
/Musique/HP+: C603.1, FB601.2, J601.1, J601.2
/Musique/HP-: C606.1, FB602.2, J601.3
GND: C601.2, C602.2, C603.2, C605.2, C606.2, RV601.3, U601.4 (IN-), U601.7 (GND); also elsewhere on the board
unnamed: C604.1, RV601.2
unnamed: C604.2, U601.3 (IN+)
unnamed: FB601.1, U601.5 (OUT+)
unnamed: FB602.1, U601.8 (OUT-)

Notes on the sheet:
AMPLI CLASSE D

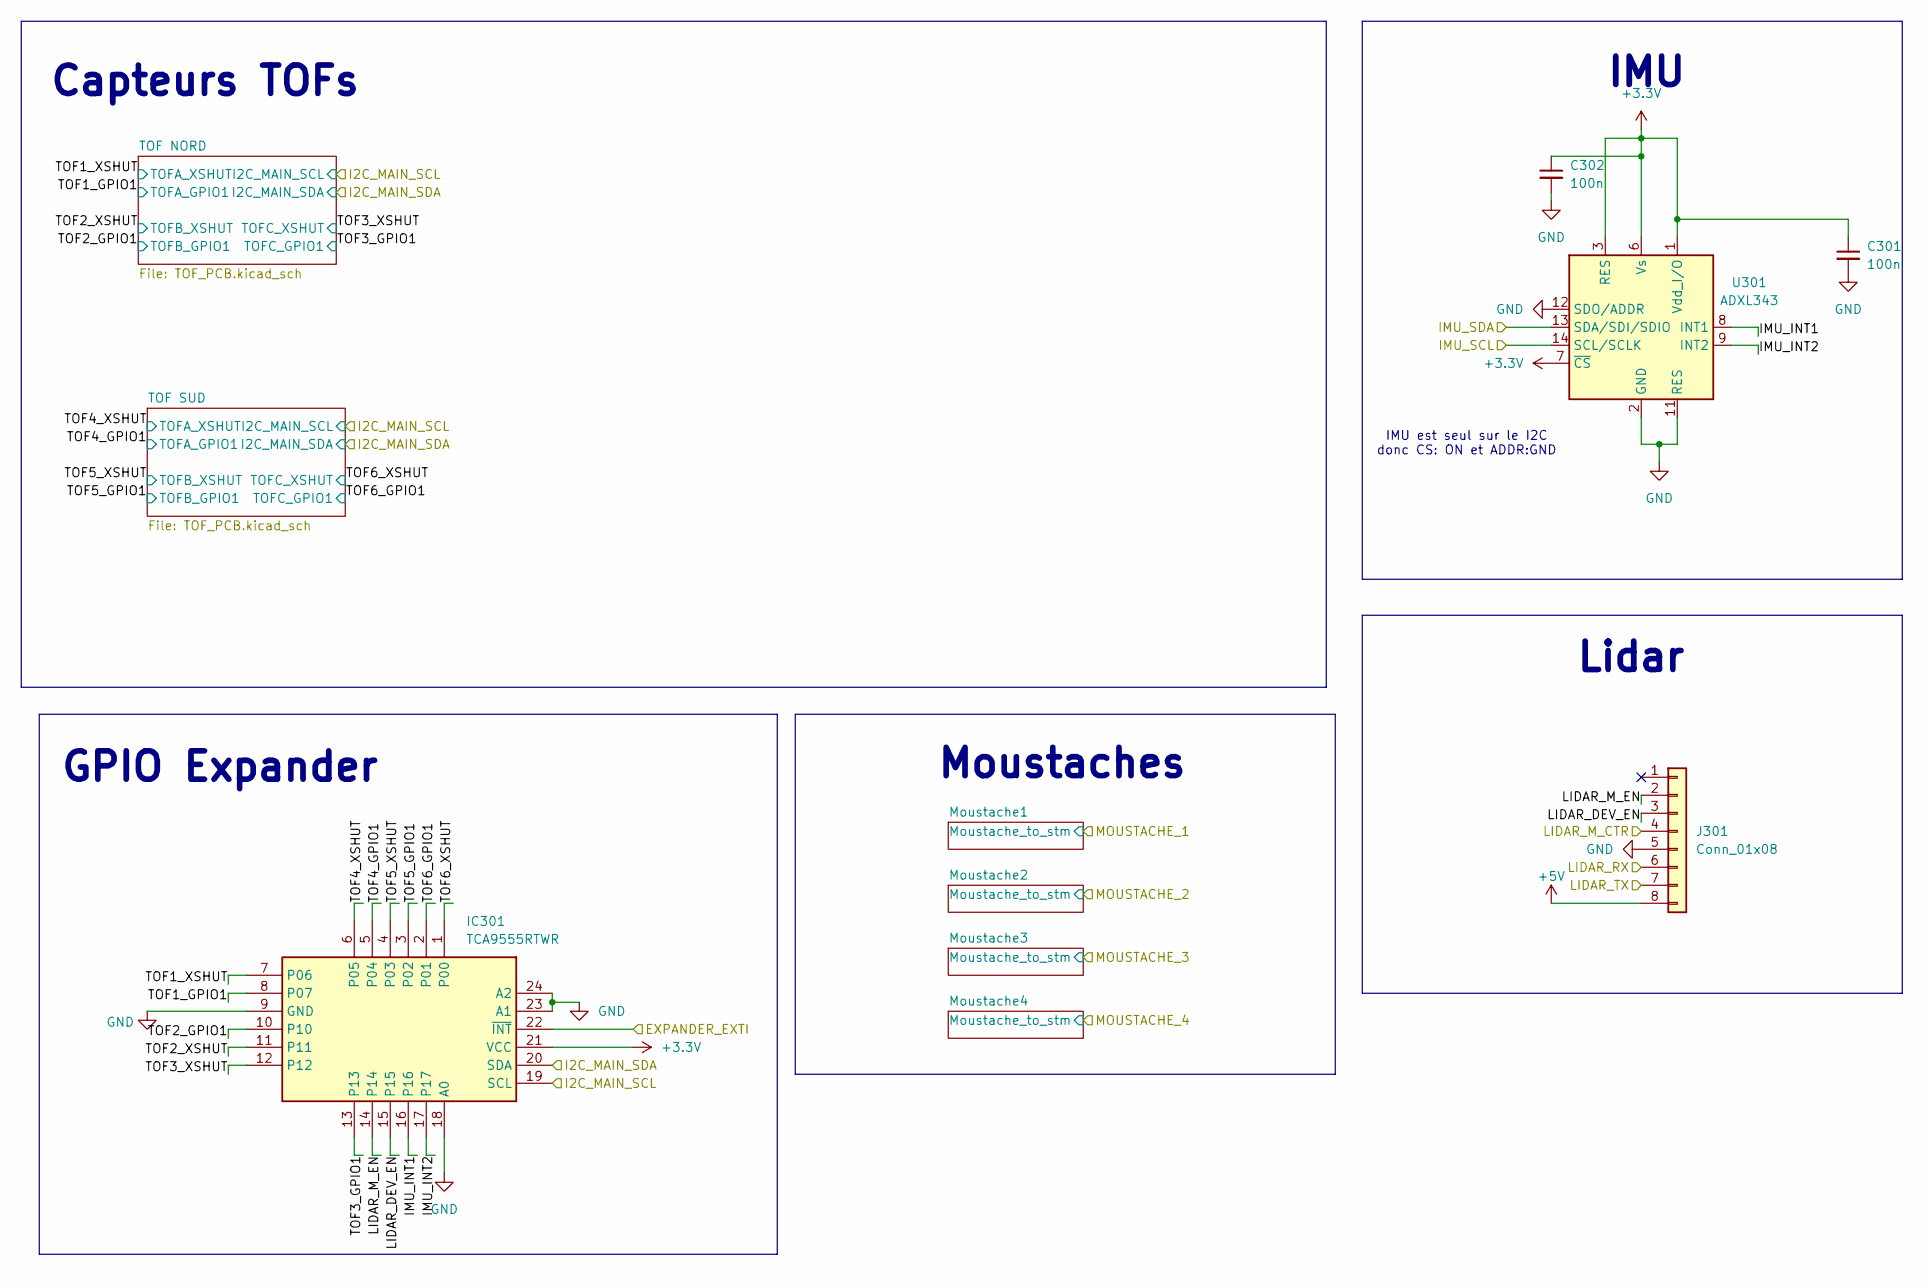
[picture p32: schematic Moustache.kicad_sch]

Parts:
C301: 100n; C_0402_1005Metric
C302: 100n; C_0603_1608Metric
IC301: TCA9555RTWR; RTW24_2P45X2P45; Manufacturer_Part_Number TCA9555RTWR; Mouser Part Number 595-TCA9555RTWR
J301: Conn_01x08; JST_XH_S8B-XH-A_1x08_P2.50mm_Horizontal
U301: ADXL343; PQFN80P300X500X100-14N

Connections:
+3.3V: C301.1, C302.1, IC301.21 (VCC), U301.1 (Vdd_I/O), U301.3 (RES), U301.6 (Vs), U301.7 (~CS); also elsewhere on the board
+5V: J301.8; also elsewhere on the board
/Led_Debug/Led_Debug_SCL: IC301.19 (SCL); also elsewhere on the board
/Led_Debug/Led_Debug_SDA: IC301.20 (SDA); also elsewhere on the board
/Périphériques/EXPANDER_EXTI: IC301.22 (~INT); also elsewhere on the board
/Périphériques/IMU_INT1: IC301.16, U301.8 (INT1)
/Périphériques/IMU_INT2: IC301.17, U301.9 (INT2)
/Périphériques/IMU_SCL: U301.14 (SCL/SCLK); also elsewhere on the board
/Périphériques/IMU_SDA: U301.13 (SDA/SDI/SDIO); also elsewhere on the board
/Périphériques/LIDAR_DEV_EN: IC301.15, J301.3
/Périphériques/LIDAR_M_CTR: J301.4; also elsewhere on the board
/Périphériques/LIDAR_M_EN: IC301.14, J301.2
/Périphériques/LIDAR_RX: J301.6; also elsewhere on the board
/Périphériques/LIDAR_TX: J301.7; also elsewhere on the board
/Périphériques/TOF1_GPIO1: IC301.8 (P07); also elsewhere on the board
/Périphériques/TOF1_XSHUT: IC301.7 (P06); also elsewhere on the board
/Périphériques/TOF2_GPIO1: IC301.10; also elsewhere on the board
/Périphériques/TOF2_XSHUT: IC301.11; also elsewhere on the board
/Périphériques/TOF3_GPIO1: IC301.13; also elsewhere on the board
/Périphériques/TOF3_XSHUT: IC301.12; also elsewhere on the board
/Périphériques/TOF4_GPIO1: IC301.5 (P04); also elsewhere on the board
/Périphériques/TOF4_XSHUT: IC301.6 (P05); also elsewhere on the board
/Périphériques/TOF5_GPIO1: IC301.3 (P02); also elsewhere on the board
/Périphériques/TOF5_XSHUT: IC301.4 (P03); also elsewhere on the board
/Périphériques/TOF6_GPIO1: IC301.2 (P01); also elsewhere on the board
/Périphériques/TOF6_XSHUT: IC301.1 (P00); also elsewhere on the board
GND: C301.2, C302.2, IC301.9 (GND), IC301.18 (A0), IC301.23 (A1), IC301.24 (A2), J301.5, U301.2 (GND), U301.4 (GND), U301.5 (GND), U301.11 (RES), U301.12 (SDO/ADDR); also elsewhere on the board

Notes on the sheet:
GPIO Expander
Moustaches
IMU
Lidar
IMU est seul sur le I2C donc CS: ON et ADDR:GND
Capteurs TOFs

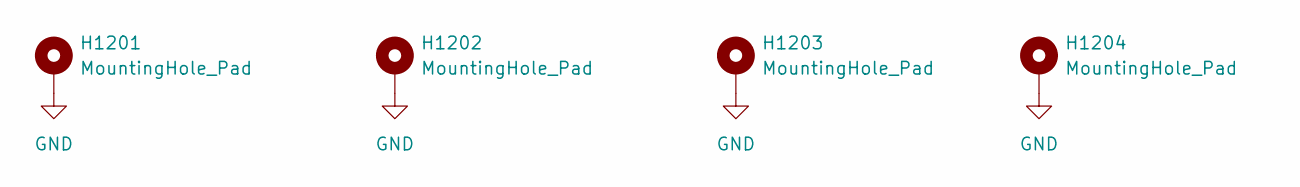
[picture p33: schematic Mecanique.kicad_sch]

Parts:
H1201, H1202, H1203, H1204: MountingHole_Pad; MountingHole_3.2mm_M3_Pad_Via

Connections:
GND: H1201.1, H1202.1, H1203.1, H1204.1; also elsewhere on the board

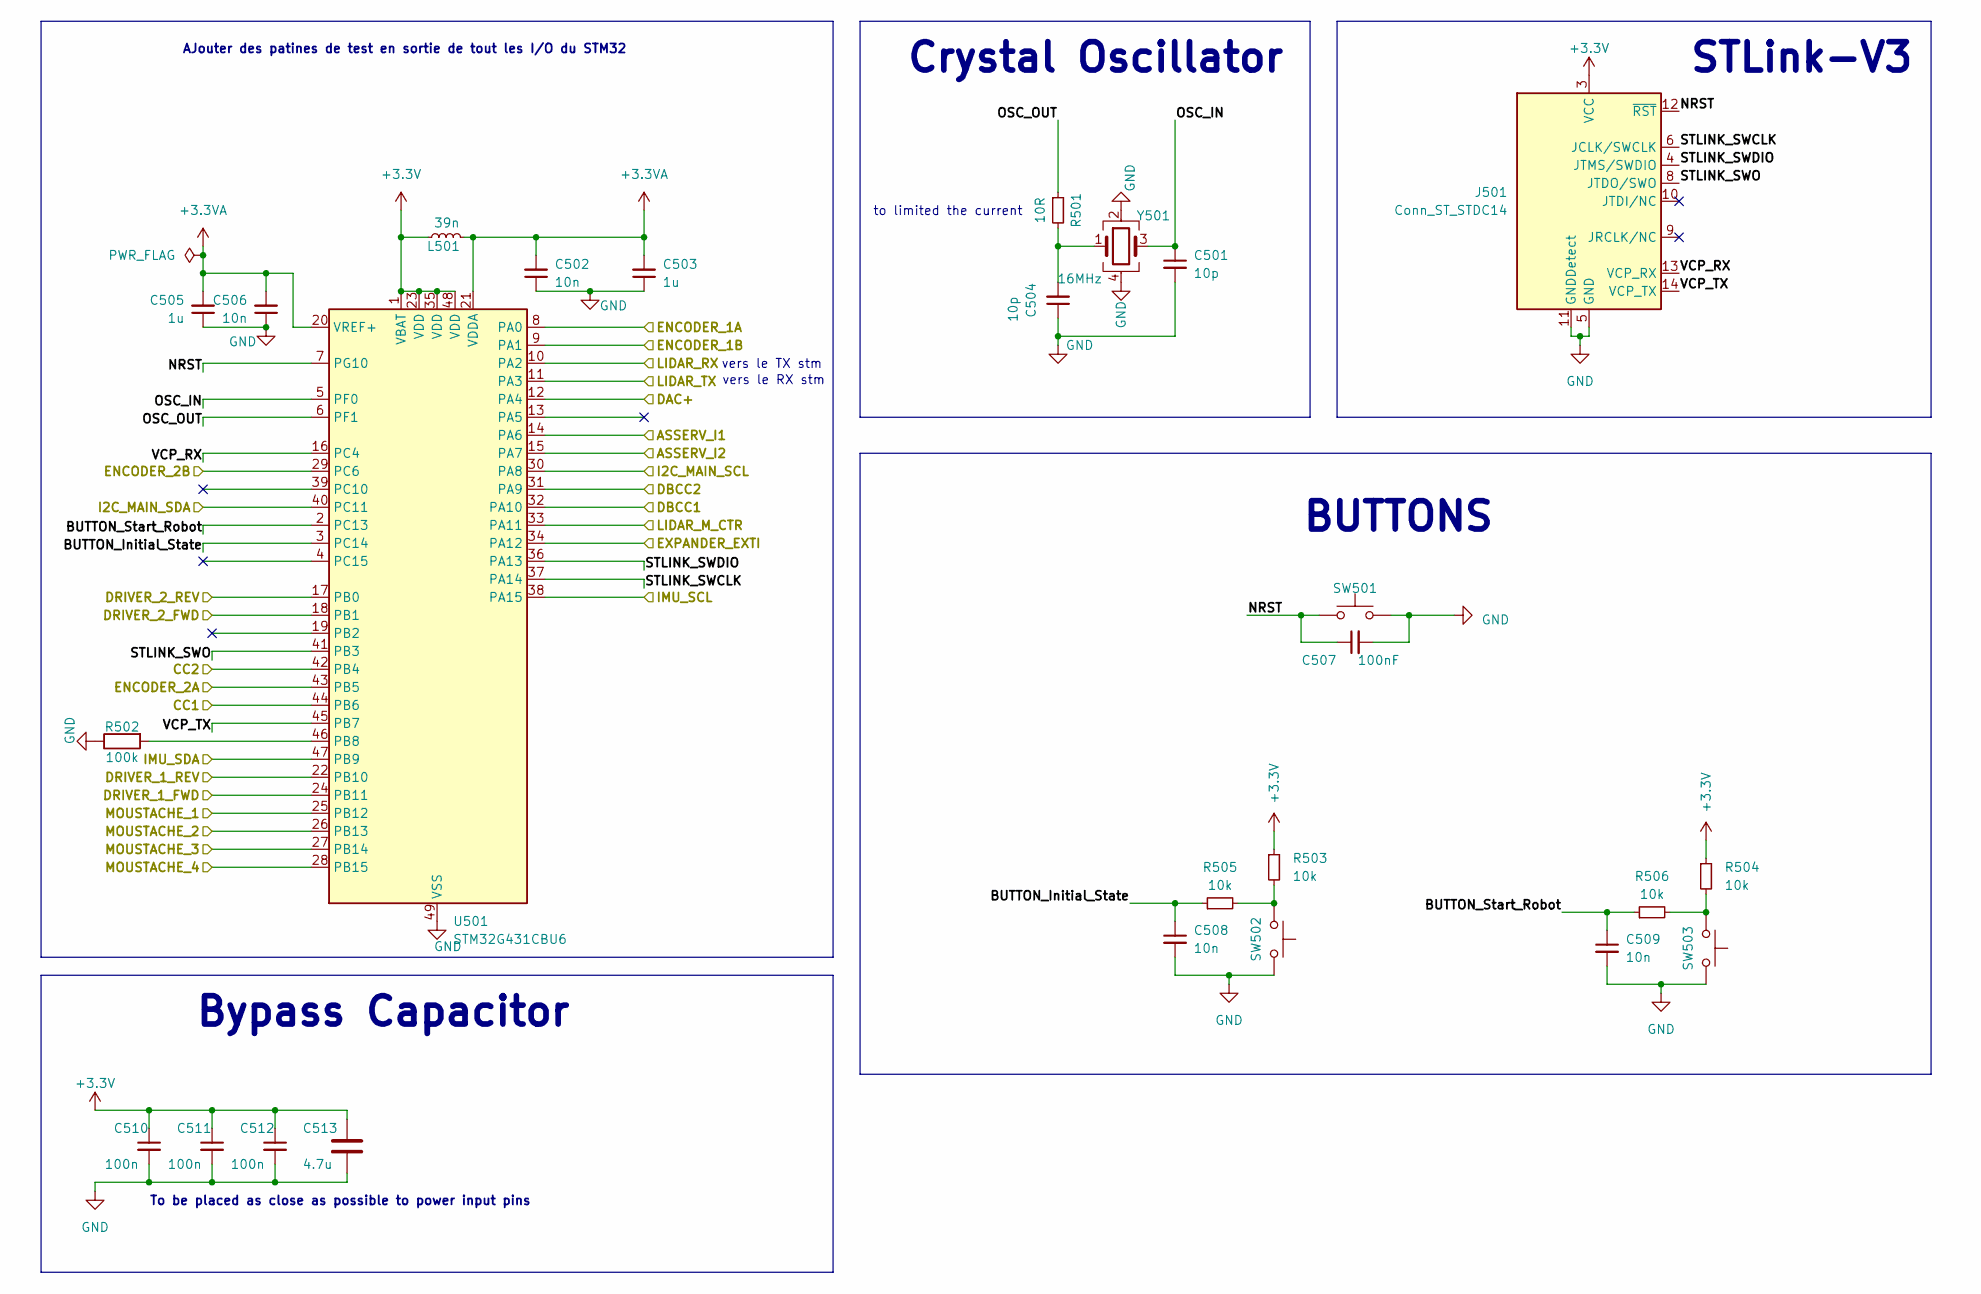
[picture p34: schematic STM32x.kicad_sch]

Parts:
C501, C504: 10p; C_0402_1005Metric
C502, C506, C508, C509: 10n; C_0402_1005Metric
C503, C505: 1u; C_0603_1608Metric
C507: 100nF; C_0402_1005Metric
C510, C511, C512: 100n; C_0402_1005Metric
C513: 4.7u; C_0603_1608Metric
J501: Conn_ST_STDC14; PinHeader_2x07_P1.27mm_Vertical_SMD
L501: 39n; WE-LQS_2512
R501: 10R; R_0402_1005Metric
R502: 100k; R_0402_1005Metric
R503, R504, R505, R506: 10k; R_0402_1005Metric
SW501, SW502, SW503: SW_Push; SW_Push_1P1T_NO_6x6mm_H9.5mm
U501: STM32G431CBU6; QFN-48-1EP_7x7mm_P0.5mm_EP5.1x5.1mm
Y501: 16MHz; Crystal_SMD_EuroQuartz_MT-4Pin_3.2x2.5mm; Mouser Part Number 2853935

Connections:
+3.3V: C510.1, C511.1, C512.1, C513.1, J501.3 (VCC), L501.2, R503.1, R504.1, U501.1 (VBAT), U501.23 (VDD), U501.35 (VDD), U501.48 (VDD); also elsewhere on the board
+3.3VA: C502.2, C503.2, C505.2, C506.2, L501.1, U501.20 (VREF+), U501.21 (VDDA)
/Alimentation/CC1: U501.32 (PA10), U501.44 (PB6); also elsewhere on the board
/Alimentation/CC2: U501.31 (PA9), U501.42 (PB4); also elsewhere on the board
/Led_Debug/Led_Debug_SCL: U501.30 (PA8); also elsewhere on the board
/Led_Debug/Led_Debug_SDA: U501.40 (PC11); also elsewhere on the board
/Motors&Drivers/ASSERV_I1: U501.14 (PA6); also elsewhere on the board
/Motors&Drivers/ASSERV_I2: U501.15 (PA7); also elsewhere on the board
/Motors&Drivers/ENCODER_1A: U501.8 (PA0); also elsewhere on the board
/Motors&Drivers/ENCODER_1B: U501.9 (PA1); also elsewhere on the board
/Motors&Drivers/ENCODER_2A: U501.43 (PB5); also elsewhere on the board
/Motors&Drivers/ENCODER_2B: U501.29 (PC6); also elsewhere on the board
/Motors&Drivers/PWM_MOT1_CH1: U501.24 (PB11); also elsewhere on the board
/Motors&Drivers/PWM_MOT1_CH2: U501.22 (PB10); also elsewhere on the board
/Motors&Drivers/PWM_MOT2_CH1: U501.18 (PB1); also elsewhere on the board
/Motors&Drivers/PWM_MOT2_CH2: U501.17 (PB0); also elsewhere on the board
/Musique/DAC_STM+: U501.12 (PA4); also elsewhere on the board
/Périphériques/EXPANDER_EXTI: U501.34 (PA12); also elsewhere on the board
/Périphériques/IMU_SCL: U501.38 (PA15); also elsewhere on the board
/Périphériques/IMU_SDA: U501.47 (PB9); also elsewhere on the board
/Périphériques/LIDAR_M_CTR: U501.33 (PA11); also elsewhere on the board
/Périphériques/LIDAR_RX: U501.10 (PA2); also elsewhere on the board
/Périphériques/LIDAR_TX: U501.11 (PA3); also elsewhere on the board
/Périphériques/MOUSTACHE_1: U501.25 (PB12); also elsewhere on the board
/Périphériques/MOUSTACHE_2: U501.26 (PB13); also elsewhere on the board
/Périphériques/MOUSTACHE_3: U501.27 (PB14); also elsewhere on the board
/Périphériques/MOUSTACHE_4: U501.28 (PB15); also elsewhere on the board
/STM32/BUTTON_Initial_State: C508.1, R505.1, U501.3 (PC14)
/STM32/BUTTON_Start_Robot: C509.1, R506.1, U501.2 (PC13)
/STM32/NRST: C507.1, J501.12 (~RST), SW501.1, U501.7 (PG10)
/STM32/OSC_IN: C501.1, U501.5 (PF0), Y501.3
/STM32/OSC_OUT: R501.1, U501.6 (PF1)
/STM32/STLINK_SWCLK: J501.6 (JCLK/SWCLK), U501.37 (PA14)
/STM32/STLINK_SWDIO: J501.4 (JTMS/SWDIO), U501.36 (PA13)
/STM32/STLINK_SWO: J501.8 (JTDO/SWO), U501.41 (PB3)
/STM32/VCP_RX: J501.13 (VCP_RX), U501.16 (PC4)
/STM32/VCP_TX: J501.14 (VCP_TX), U501.45 (PB7)
GND: C501.2, C502.1, C503.1, C504.1, C505.1, C506.1, C507.2, C508.2, C509.2, C510.2, C511.2, C512.2, C513.2, J501.5 (GND), J501.7 (GND), J501.11 (GNDDetect), R502.1, SW501.2, SW502.1, SW503.1, U501.49 (VSS), Y501.2, Y501.4; also elsewhere on the board
unnamed: C504.2, R501.2, Y501.1
unnamed: R503.2, R505.2, SW502.2
unnamed: R504.2, R506.2, SW503.2
unnamed: R502.2, U501.46 (PB8)

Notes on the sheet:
Bypass Capacitor
to limited the current
vers le TX stm
vers le RX stm
BUTTONS
AJouter des patines de test en sortie de tout les I/O du STM32
To be placed as close as possible to power input pins
Crystal Oscillator
STLink-V3

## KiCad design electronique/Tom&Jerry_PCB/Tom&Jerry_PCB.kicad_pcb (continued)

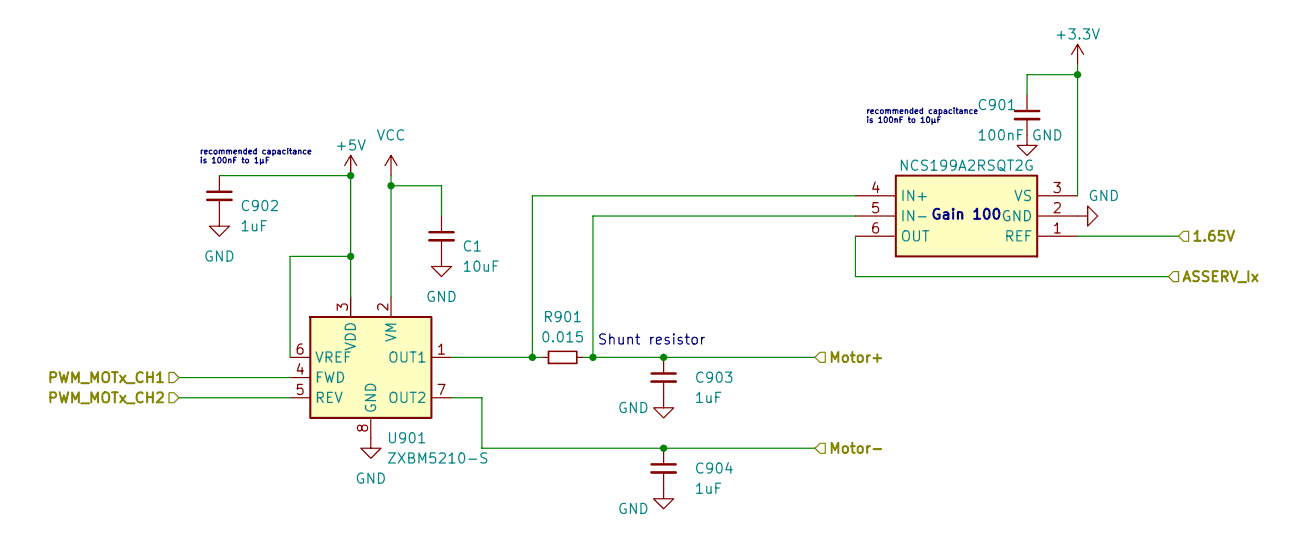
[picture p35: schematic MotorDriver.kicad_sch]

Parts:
C1: 10uF; C_0603_1608Metric
C901: 100nF; C_0402_1005Metric
C902, C903, C904: 1uF; C_0603_1608Metric
IC901: NCS199A2RSQT2G; SOT65P210X110-6N; Mouser Part Number 863-NCS199A2RSQT2G
R901: 0.015; R_0805_2012Metric
U901: ZXBM5210-S; XBM5210; Mouser Part Number 621-ZXBM5210-SP-13

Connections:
1.65V: IC901.1 (REF); also elsewhere on the board
+3.3V: C901.1, IC901.3 (VS); also elsewhere on the board
+5V: C902.1, U901.3 (VDD), U901.6 (VREF); also elsewhere on the board
/Motors&Drivers/ASSERV_I1: IC901.6 (OUT); also elsewhere on the board
/Motors&Drivers/Motor1+: C903.1, IC901.5 (IN-), R901.2; also elsewhere on the board
/Motors&Drivers/Motor1-: C904.1, U901.7 (OUT2); also elsewhere on the board
/Motors&Drivers/PWM_MOT1_CH1: U901.4 (FWD); also elsewhere on the board
/Motors&Drivers/PWM_MOT1_CH2: U901.5 (REV); also elsewhere on the board
GND: C1.2, C901.2, C902.2, C903.2, C904.2, IC901.2 (GND), U901.8 (GND); also elsewhere on the board
unnamed: IC901.4 (IN+), R901.1, U901.1 (OUT1)
VCC: C1.1, U901.2 (VM); also elsewhere on the board

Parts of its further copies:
C2: 10uF; C_0603_1608Metric
C1101: 100nF; C_0402_1005Metric
C1102, C1103, C1104: 1uF; C_0603_1608Metric
IC1101: NCS199A2RSQT2G; SOT65P210X110-6N; Mouser Part Number 863-NCS199A2RSQT2G
R1101: 0.015; R_0805_2012Metric
U1101: ZXBM5210-S; XBM5210; Mouser Part Number 621-ZXBM5210-SP-13

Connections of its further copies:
1.65V: IC1101.1 (REF); also elsewhere on the board
+3.3V: C1101.1, IC1101.3 (VS); also elsewhere on the board
+5V: C1102.1, U1101.3 (VDD), U1101.6 (VREF); also elsewhere on the board
/Motors&Drivers/ASSERV_I2: IC1101.6 (OUT); also elsewhere on the board
/Motors&Drivers/Motor2+: C1103.1, IC1101.5 (IN-), R1101.2; also elsewhere on the board
/Motors&Drivers/Motor2-: C1104.1, U1101.7 (OUT2); also elsewhere on the board
/Motors&Drivers/PWM_MOT2_CH1: U1101.4 (FWD); also elsewhere on the board
/Motors&Drivers/PWM_MOT2_CH2: U1101.5 (REV); also elsewhere on the board
GND: C2.2, C1101.2, C1102.2, C1103.2, C1104.2, IC1101.2 (GND), U1101.8 (GND); also elsewhere on the board
unnamed: IC1101.4 (IN+), R1101.1, U1101.1 (OUT1)
VCC: C2.1, U1101.2 (VM); also elsewhere on the board

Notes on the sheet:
recommended capacitance is 100nF to 1μF
Gain 100
recommended capacitance is 100nF to 10μF
Shunt resistor

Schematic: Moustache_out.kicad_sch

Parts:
C1701: 10n; C_0402_1005Metric
J1701: Conn_01x02; JST_XH_S2B-XH-A-1_1x02_P2.50mm_Horizontal
R1701, R1702: 10k; R_0402_1005Metric

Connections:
+3.3V: R1701.1; also elsewhere on the board
/Périphériques/MOUSTACHE_4: C1701.1, R1702.1; also elsewhere on the board
GND: C1701.2, J1701.2; also elsewhere on the board
unnamed: J1701.1, R1701.2, R1702.2

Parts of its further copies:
C1301, C1501, C1601: 10n; C_0402_1005Metric
J1301, J1501, J1601: Conn_01x02; JST_XH_S2B-XH-A-1_1x02_P2.50mm_Horizontal
R1301, R1302, R1501, R1502, R1601, R1602: 10k; R_0402_1005Metric

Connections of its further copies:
+3.3V: R1301.1, R1501.1, R1601.1; also elsewhere on the board
/Périphériques/MOUSTACHE_1: C1301.1, R1302.1; also elsewhere on the board
/Périphériques/MOUSTACHE_2: C1501.1, R1502.1; also elsewhere on the board
/Périphériques/MOUSTACHE_3: C1601.1, R1602.1; also elsewhere on the board
GND: C1301.2, C1501.2, C1601.2, J1301.2, J1501.2, J1601.2; also elsewhere on the board
unnamed: J1301.1, R1301.2, R1302.2
unnamed: J1501.1, R1501.2, R1502.2
unnamed: J1601.1, R1601.2, R1602.2

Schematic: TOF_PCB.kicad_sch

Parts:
J1001: FTSH-105-01-F-DV-P-TR; SAMTEC_FTSH-105-01-F-DV-P-TR; PARTREV R

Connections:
+5V: J1001.05; also elsewhere on the board
/Led_Debug/Led_Debug_SCL: J1001.02; also elsewhere on the board
/Led_Debug/Led_Debug_SDA: J1001.04; also elsewhere on the board
/Périphériques/TOF1_GPIO1: J1001.03; also elsewhere on the board
/Périphériques/TOF1_XSHUT: J1001.01; also elsewhere on the board
/Périphériques/TOF2_GPIO1: J1001.09; also elsewhere on the board
/Périphériques/TOF2_XSHUT: J1001.07; also elsewhere on the board
/Périphériques/TOF3_GPIO1: J1001.10; also elsewhere on the board
/Périphériques/TOF3_XSHUT: J1001.08; also elsewhere on the board
GND: J1001.06; also elsewhere on the board

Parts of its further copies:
J701: FTSH-105-01-F-DV-P-TR; SAMTEC_FTSH-105-01-F-DV-P-TR; PARTREV R

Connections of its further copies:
+5V: J701.05; also elsewhere on the board
/Led_Debug/Led_Debug_SCL: J701.02; also elsewhere on the board
/Led_Debug/Led_Debug_SDA: J701.04; also elsewhere on the board
/Périphériques/TOF4_GPIO1: J701.03; also elsewhere on the board
/Périphériques/TOF4_XSHUT: J701.01; also elsewhere on the board
/Périphériques/TOF5_GPIO1: J701.09; also elsewhere on the board
/Périphériques/TOF5_XSHUT: J701.07; also elsewhere on the board
/Périphériques/TOF6_GPIO1: J701.10; also elsewhere on the board
/Périphériques/TOF6_XSHUT: J701.08; also elsewhere on the board
GND: J701.06; also elsewhere on the board

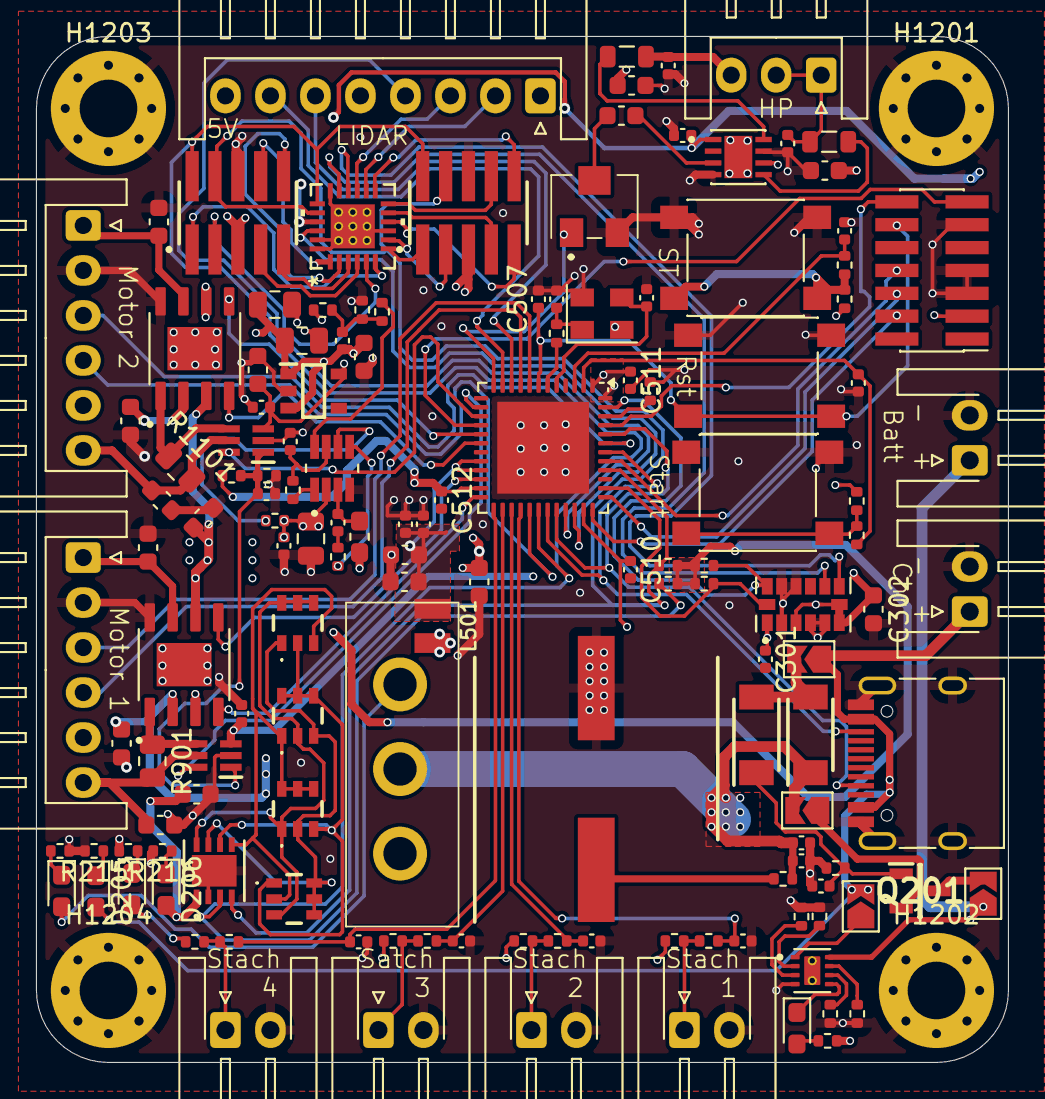
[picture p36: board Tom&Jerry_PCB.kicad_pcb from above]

Board: 4 copper layers, 54.0 x 57.0 mm, 144 parts (0 on the bottom side), 108 nets.

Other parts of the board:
LED801, LED802, LED803, LED804: RGB; 5988G10313F
U801: LP5812ADSDR; WSON8_DSD_TEX

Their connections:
+5V: U801.1 (VCC); also elsewhere on the board
/Led_Debug/Led_Debug_SCL: U801.3 (SCL); also elsewhere on the board
/Led_Debug/Led_Debug_SDA: U801.4 (SDA); also elsewhere on the board
GND: U801.2 (SYNC), U801.9 (GND); also elsewhere on the board
unnamed: LED801.5 (B+), LED802.3 (G+), LED803.2 (R-), LED803.4 (G-), LED803.6 (B-), LED804.1 (R+), U801.5 (OUT3)
unnamed: LED801.2 (R-), LED801.4 (G-), LED801.6 (B-), LED802.5 (B+), LED803.1 (R+), LED804.3 (G+), U801.8 (OUT0)
unnamed: LED801.3 (G+), LED802.1 (R+), LED803.5 (B+), LED804.2 (R-), LED804.4 (G-), LED804.6 (B-), U801.6 (OUT2)
unnamed: LED801.1 (R+), LED802.2 (R-), LED802.4 (G-), LED802.6 (B-), LED803.3 (G+), LED804.5 (B+), U801.7 (OUT1)

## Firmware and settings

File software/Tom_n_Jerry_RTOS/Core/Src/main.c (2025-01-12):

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
/* Includes ------------------------------------------------------------------*/
#include "main.h"
#include "cmsis_os.h"
#include "adc.h"
#include "dac.h"
#include "dma.h"
#include "i2c.h"
#include "tim.h"
#include "ucpd.h"
#include "usart.h"
#include "usbpd.h"
#include "gpio.h"

/* USER CODE BEGIN Includes */
#include "callBack.h"
#include "asserv.h"
#include "changeMode.h"
#include "lidar.h"
#include "init.h"

/* USER CODE END Includes */

/* USER CODE BEGIN PD */
#define TASK_STACK_DEPTH_SHELL 2048
#define TASK_PRIORITY_SHELL 2

#define TASK_STACK_DEPTH_ASSERV_I 64
#define TASK_PRIORITY_ASSERV_I 2

#define TASK_STACK_DEPTH_ASSERV_XYZ 64
#define TASK_PRIORITY_ASSERV_XYZ 3

#define TASK_STACK_DEPTH_CHANGEMODE 64
#define TASK_PRIORITY_CHANGEMODE 10

#define TASK_STACK_DEPTH_LIDAR 512
#define TASK_PRIORITY_LIDAR 5
/* USER CODE END PD */


/* USER CODE BEGIN PV */
HeapStats_t heapStats;

TaskHandle_t h_task_shell = NULL;
TaskHandle_t h_task_asserv_I = NULL;
TaskHandle_t h_task_asserv_XYZ = NULL;
TaskHandle_t h_task_changemenMode = NULL;
TaskHandle_t h_task_init= NULL;
TaskHandle_t h_task_LIDAR_Take = NULL;
TaskHandle_t h_task_LIDAR_Process = NULL;


SemaphoreHandle_t semb_halfCllbck;
SemaphoreHandle_t semb_cpltCllbck;

/* USER CODE END PV */

void SystemClock_Config(void);
void MX_FREERTOS_Init(void);
/**
  * @brief  The application entry point.
  * @retval int
  */
int main(void)
{

  /* MCU Configuration--------------------------------------------------------*/

  /* Reset of all peripherals, Initializes the Flash interface and the Systick. */
  HAL_Init();

  /* Configure the system clock */
  SystemClock_Config();

  /* Initialize all configured peripherals */
  MX_GPIO_Init();
  MX_DMA_Init();
  MX_ADC2_Init();
  MX_DAC1_Init();
  MX_I2C1_Init();
  MX_I2C3_Init();
  MX_TIM2_Init();
  MX_TIM3_Init();
  MX_TIM4_Init();
  MX_UCPD1_Init();
  MX_USART1_UART_Init();
  MX_USART2_UART_Init();
  MX_TIM15_Init();
  MX_TIM16_Init();
  MX_TIM6_Init();
  MX_TIM7_Init();
  /* USER CODE BEGIN 2 */

	semb_cpltCllbck = xSemaphoreCreateBinary();
	semb_halfCllbck = xSemaphoreCreateBinary();

	shell_init();
	lidar_init();
	changement_mode_init();

	vPortGetHeapStats(&heapStats);
	//xTaskCreate(init_run , 				"Initalisation",TASK_STACK_DEPTH_CHANGEMODE, NULL, 1, &h_task_init) != pdPASS ? Error_Handler():(void)0;
	vPortGetHeapStats(&heapStats);
	xTaskCreate(changeMode_run,			"Changement MODE", TASK_STACK_DEPTH_CHANGEMODE, NULL, TASK_PRIORITY_CHANGEMODE, &h_task_changemenMode) != pdPASS ? Error_Handler():(void)0;
	//vPortGetHeapStats(&heapStats);
	xTaskCreate(asserv_courant_run, 	"Asserv Courant", TASK_STACK_DEPTH_ASSERV_I, NULL, TASK_PRIORITY_ASSERV_I, &h_task_asserv_I) != pdPASS ? Error_Handler():(void)0;
	vPortGetHeapStats(&heapStats);
	//xTaskCreate(asserv_position_run, 	"Asserv Position", TASK_STACK_DEPTH_ASSERV_XYZ, NULL, TASK_PRIORITY_ASSERV_XYZ, &h_task_asserv_XYZ) != pdPASS ? Error_Handler():(void)0;
	vPortGetHeapStats(&heapStats);

	xTaskCreate(lidarprocess,			"LIDAR_Process", TASK_STACK_DEPTH_LIDAR, NULL, TASK_PRIORITY_LIDAR, &h_task_LIDAR_Process) != pdPASS ? Error_Handler():(void)0;
	vPortGetHeapStats(&heapStats);
	xTaskCreate(lidarTake,				"LIDAR_Take", TASK_STACK_DEPTH_LIDAR, NULL, TASK_PRIORITY_LIDAR+1, &h_task_LIDAR_Take) != pdPASS ? Error_Handler():(void)0;
	vPortGetHeapStats(&heapStats);
	xTaskCreate(shell_run,				"Shell", TASK_STACK_DEPTH_SHELL, NULL, TASK_PRIORITY_SHELL, &h_task_shell) != pdPASS ? Error_Handler():(void)0;
	vPortGetHeapStats(&heapStats);
	osKernelStart();
  /* USER CODE END 2 */

  /* USBPD initialisation ---------------------------------*/
  MX_USBPD_Init();

  /* Call init function for freertos objects (in cmsis_os2.c) */
  MX_FREERTOS_Init();

  /* Start scheduler */
  osKernelStart();

  /* We should never get here as control is now taken by the scheduler */

  /* Infinite loop */
  /* USER CODE BEGIN WHILE */
	while (1)
	{
    /* USER CODE END WHILE */

    /* USER CODE BEGIN 3 */
	}
  /* USER CODE END 3 */
}

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
/**
  * @brief  Period elapsed callback in non blocking mode
  * @note   This function is called  when TIM17 interrupt took place, inside
  * HAL_TIM_IRQHandler(). It makes a direct call to HAL_IncTick() to increment
  * a global variable "uwTick" used as application time base.
  * @param  htim : TIM handle
  * @retval None
  */
void HAL_TIM_PeriodElapsedCallback(TIM_HandleTypeDef *htim)
{
  /* USER CODE BEGIN Callback 0 */
	CUSTOM_TIM_PeriodElapsedCallback(htim);
  /* USER CODE END Callback 0 */
  if (htim->Instance == TIM17) {
    HAL_IncTick();
  }
}

/**
  * @brief  This function is executed in case of error occurrence.
  * @retval None
  */
void Error_Handler(void)
{
  /* USER CODE BEGIN Error_Handler_Debug */
	/* User can add his own implementation to report the HAL error return state */
	__disable_irq();
	while (1)
	{
	}
  /* USER CODE END Error_Handler_Debug */
}

#ifdef  USE_FULL_ASSERT
/**
  * @brief  Reports the name of the source file and the source line number
  *         where the assert_param error has occurred.
  * @param  file: pointer to the source file name
  * @param  line: assert_param error line source number
  * @retval None
  */
void assert_failed(uint8_t *file, uint32_t line)
{
  /* USER CODE BEGIN 6 */
	/* User can add his own implementation to report the file name and line number,
     ex: printf("Wrong parameters value: file %s on line %d\r\n", file, line) */
  /* USER CODE END 6 */
}
#endif /* USE_FULL_ASSERT */

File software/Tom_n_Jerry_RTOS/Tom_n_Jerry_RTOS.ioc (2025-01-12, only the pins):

Mcu.UserName=STM32G431CBUx
PA10.Signal=UCPD1_DBCC2
PA11.GPIO_Label=LIDAR_M_CTR
PA11.Signal=GPIO_Output
PA12.GPIO_Label=GE_EXTI
PA12.Signal=GPXTI12
PA13.Signal=SYS_JTMS-SWDIO
PA14.Signal=SYS_JTCK-SWCLK
PA15.GPIO_Label=I2C_IMU_SCL
PA15.Signal=I2C1_SCL
PA2.GPIO_Label=LIDAR_RXnTX_STM
PA2.Signal=USART2_TX
PA3.GPIO_Label=LIDAR_TXnRX_STM
PA3.Signal=USART2_RX
PA4.GPIO_Label=DAC+
PA4.Signal=COMP_DAC11_group
PA6.GPIO_Label=ASSERV_I1
PA6.Signal=ADC2_IN3
PA7.GPIO_Label=ASSERV_I2
PA7.Signal=ADC2_IN4
PA8.GPIO_Label=I2C_MAIN_SCL
PA8.Signal=I2C3_SCL
PA9.Signal=UCPD1_DBCC1
PB0.GPIO_Label=DRIVER_FWD2
PB0.Signal=S_TIM3_CH3
PB1.GPIO_Label=DRIVER_REV2
PB1.Signal=S_TIM3_CH4
PB10.GPIO_Label=DRIVER_REV1
PB10.Signal=S_TIM2_CH3
PB11.GPIO_Label=DRIVER_FWD1
PB11.Signal=S_TIM2_CH4
PB13.GPIO_Label=MOUSTACHE_3
PB13.Signal=GPIO_Input
PB14.GPIO_Label=START
PB14.Signal=GPXTI14
PB15.GPIO_Label=MOUSTACHE_1
PB15.Signal=GPIO_Input
PB3.Signal=SYS_JTDO-SWO
PB4.Signal=UCPD1_CC2
PB6.Signal=UCPD1_CC1
PB7.GPIO_Label=VCP_RX
PB7.Signal=USART1_RX
PB9.GPIO_Label=I2C_IMU_SDA
PB9.Signal=I2C1_SDA
PC11.GPIO_Label=I2C_MAIN_SDA
PC11.Signal=I2C3_SDA
PC4.GPIO_Label=VCP_TX
PC4.Signal=USART1_TX
PF0-OSC_IN.Signal=RCC_OSC_IN
PF1-OSC_OUT.Signal=RCC_OSC_OUT

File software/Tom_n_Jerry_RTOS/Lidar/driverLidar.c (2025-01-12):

/*
 * driverLidar.c
 *
 *  Created on: Dec 11, 2024
 *      Author: romingo
 */



#include "lidar.h"
#include "shell.h"
#define MIN_DISTANCE 40 //mm

//Stop and stop scanning
int LIDAR_stop(h_LIDAR_t *h_LIDAR) {
	uint8_t cmd_buff[CMD_BUFF_SIZE] = {CMD_BEGIN, CMD_STOP}; // Commande pour arrêter le LIDAR

	// Envoi de la commande pour arrêter le LIDAR
	if (h_LIDAR->serial_drv.it_transmit(cmd_buff, CMD_BUFF_SIZE) != 0) {
		printf("Erreur lors de l'envoi de la commande.\r\n");
		return -1;
	}

	// Attente que la transmission soit terminée
	uint32_t start_time = HAL_GetTick();
	while (!h_LIDAR->rx_flag_uart) {
		if (HAL_GetTick() - start_time > 1000) { // Timeout après 1000 ms
			printf("Timeout lors de la transmission UART.\r\n");
			return -2;
		}
	}

	return 0; // Commande envoyée avec succès
}

//Soft restart
//No response
int LIDAR_restart(h_LIDAR_t * h_LIDAR){
	debug(START,"RESTART LIDAR");
	uint8_t cmd_buff[CMD_BUFF_SIZE]={CMD_BEGIN,CMD_RESTART};
	// Envoi de la commande pour restart le LIDAR
	if (h_LIDAR->serial_drv.it_transmit(cmd_buff, CMD_BUFF_SIZE) != 0) {
		printf("Erreur lors de l'envoi de la commande.\r\n");
		return -1;
	}

	return 0;
}

int LIDAR_get_info(h_LIDAR_t *h_LIDAR) {
	uint8_t cmd_buff[CMD_BUFF_SIZE] = {CMD_BEGIN, CMD_INFO};

	// Envoi de la commande pour obtenir les informations
	if (h_LIDAR->serial_drv.it_transmit(cmd_buff, CMD_BUFF_SIZE) != 0) {
		printf("Erreur lors de l'envoi de la commande.\r\n");
		return -1;
	}

	// Préparation à la réception
	h_LIDAR->rx_flag_uart = 0; // Réinitialise le drapeau
	if (h_LIDAR->serial_drv.it_receive(h_LIDAR->info_buff, INFO_BUFF_SIZE) != 0) {
		printf("Erreur lors de la preparation de la réception.\r\n");
		return -2;
	}

	// Attente de la réception
	uint32_t start_time = HAL_GetTick();
	while (!h_LIDAR->rx_flag_uart) {
		if (HAL_GetTick() - start_time > 10000) { // Timeout de 1000 ms
			printf("Timeout lors de la reception.\r\n");
			return -3;
		}
	}

	// Analyse des données
	h_LIDAR->device_info.start_sign = (h_LIDAR->info_buff[0] << 8) | h_LIDAR->info_buff[1];
	h_LIDAR->device_info.length = (h_LIDAR->info_buff[2]) |
			(h_LIDAR->info_buff[3] << 8) |
			(h_LIDAR->info_buff[4] << 16);
	h_LIDAR->device_info.mode = h_LIDAR->info_buff[5] >> 6;
	h_LIDAR->device_info.type_code = h_LIDAR->info_buff[6];

	if (h_LIDAR->device_info.start_sign != 0xA55A) {
		printf("Signature de debut invalide : %04X\r\n", h_LIDAR->device_info.start_sign);
		return -4;
	}

	if (h_LIDAR->device_info.type_code != 0x04) {
		printf("Type code invalide : %X\r\n", h_LIDAR->device_info.type_code);
		return -5;
	}

	// Récupération des autres informations
	h_LIDAR->device_info.model = h_LIDAR->info_buff[7];
	snprintf(h_LIDAR->device_info.firmware, sizeof(h_LIDAR->device_info.firmware),
			"%d.%d", h_LIDAR->info_buff[8], h_LIDAR->info_buff[9]);
	h_LIDAR->device_info.hardware = h_LIDAR->info_buff[10];
	snprintf(h_LIDAR->device_info.serial, sizeof(h_LIDAR->device_info.serial),
			"%02X%02X%02X%02X%02X%02X%02X%02X%02X%02X%02X%02X%02X%02X%02X%02X",
			h_LIDAR->info_buff[11], h_LIDAR->info_buff[12], h_LIDAR->info_buff[13], h_LIDAR->info_buff[14],
			h_LIDAR->info_buff[15], h_LIDAR->info_buff[16], h_LIDAR->info_buff[17], h_LIDAR->info_buff[18],
			h_LIDAR->info_buff[19], h_LIDAR->info_buff[20], h_LIDAR->info_buff[21], h_LIDAR->info_buff[22],
			h_LIDAR->info_buff[23], h_LIDAR->info_buff[24], h_LIDAR->info_buff[25], h_LIDAR->info_buff[26]);


	// Affichage des informations
	printf("Start sign : %04X\r\n", h_LIDAR->device_info.start_sign);
	printf("Length : %lu\r\n", h_LIDAR->device_info.length);
	printf("Mode : %X\r\n", h_LIDAR->device_info.mode);
	printf("Type code : %X\r\n", h_LIDAR->device_info.type_code);
	printf("Model : %X\r\n", h_LIDAR->device_info.model);
	printf("Firmware version : %s\r\n", h_LIDAR->device_info.firmware);
	printf("Hardware version : %u\r\n", h_LIDAR->device_info.hardware);
	printf("Serial number : %s\r\n", h_LIDAR->device_info.serial);

	return 0;
}


int LIDAR_get_health_stat(h_LIDAR_t *h_LIDAR) {
	uint8_t cmd_buff[CMD_BUFF_SIZE] = {CMD_BEGIN, CMD_HEALTH};

	// Envoi de la commande pour obtenir l'état de santé
	if (h_LIDAR->serial_drv.it_transmit(cmd_buff, CMD_BUFF_SIZE) != 0) {
		printf("Erreur lors de l'envoi de la commande.\r\n");
		return -1;
	}

	// Préparation à la réception
	h_LIDAR->rx_flag_uart = 0; // Réinitialise le drapeau
	if (h_LIDAR->serial_drv.it_receive(h_LIDAR->health_buff, HEALTH_BUFF_SIZE) != 0) {
		printf("Erreur lors de la préparation de la réception.\r\n");
		return -2;
	}

	// Attente de la réception
	uint32_t start_time = HAL_GetTick();
	while (!h_LIDAR->rx_flag_uart) {
		if (HAL_GetTick() - start_time > 1000) { // Timeout de 1000 ms
			printf("Timeout lors de la reception.\r\n");
			return -3;
		}
	}

	// Analyse des données
	h_LIDAR->health_stat.start_sign = (h_LIDAR->health_buff[0] << 8) | h_LIDAR->health_buff[1];
	h_LIDAR->health_stat.length = (h_LIDAR->health_buff[2]) |
			(h_LIDAR->health_buff[3] << 8) |
			(h_LIDAR->health_buff[4] << 16);
	h_LIDAR->health_stat.mode = h_LIDAR->health_buff[5] >> 6;
	h_LIDAR->health_stat.type_code = h_LIDAR->health_buff[6];
	h_LIDAR->health_stat.status_code = h_LIDAR->health_buff[7];
	h_LIDAR->health_stat.error_code = h_LIDAR->health_buff[8] | (h_LIDAR->health_buff[9] << 8);

	if (h_LIDAR->health_stat.start_sign != 0xA55A) {
		printf("Signature de debut invalide : %04X\r\n", h_LIDAR->health_stat.start_sign);
		return -4;
	}

	if (h_LIDAR->health_stat.type_code != 0x06) {
		printf("Type code invalide : %X\r\n", h_LIDAR->health_stat.type_code);
		return -5;
	}

	// Affichage de l'état de santé
	printf("Start sign : %04X\r\n", h_LIDAR->health_stat.start_sign);
	printf("Length : %lu\r\n", h_LIDAR->health_stat.length);
	printf("Mode : %X\r\n", h_LIDAR->health_stat.mode);
	printf("Type code : %X\r\n", h_LIDAR->health_stat.type_code);
	printf("Status code : %02X\r\n", h_LIDAR->health_stat.status_code);
	printf("Error code : %04X\r\n", h_LIDAR->health_stat.error_code);

	return 0;
}

int LIDAR_start_scan_dma(h_LIDAR_t *h_LIDAR) {
	uint8_t cmd_buff[CMD_BUFF_SIZE] = {CMD_BEGIN, CMD_START}; // Commande pour démarrer le scan

	// Envoi de la commande
	if (h_LIDAR->serial_drv.it_transmit(cmd_buff, CMD_BUFF_SIZE) != 0) {
		printf("Erreur lors de l'envoi de la commande de démarrage du scan.\r\n");
		return -1;
	}

	// Configurer la réception DMA en mode circulaire
	if (h_LIDAR->serial_drv.dma_receive(h_LIDAR->processing.receive_buff, DATA_BUFF_SIZE) != 0) {
		printf("Erreur lors de la configuration de la réception DMA.\r\n");
		return -2;
	}

	printf("Scan DMA demarre avec succes en mode circulaire.\r\n");
	return 0;
}
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

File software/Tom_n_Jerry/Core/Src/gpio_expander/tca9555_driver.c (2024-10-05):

/**
 * @author Alexander Grin
 * @copyright (C) 2020 Grin Development. All rights reserved.
 *
 * https://github.com/DimaSes99/tca9555_driver/tree/master
 *
 */

#include "gpio_Expander/tca9555_driver.h"

/****************************** Common macros ********************************/
/** C standard macros */
#ifndef NULL
#ifdef __cplusplus
#define NULL                                (0)
#else
#define NULL                                ((void *) 0)
#endif
#endif

/** Define Endian-ness */
#ifndef __ORDER_LITTLE_ENDIAN__
#define __ORDER_LITTLE_ENDIAN__             (0)
#endif

#ifndef __BYTE_ORDER__
#define __BYTE_ORDER__                      __ORDER_LITTLE_ENDIAN__
#endif

#if __BYTE_ORDER__ == __ORDER_LITTLE_ENDIAN__
#ifndef LITTLE_ENDIAN
#define LITTLE_ENDIAN                       (1)
#endif
#elif __BYTE_ORDER__ == __ORDER_BIG_ENDIAN__
#ifndef BIG_ENDIAN
#define BIG_ENDIAN                          (1)
#endif
#endif

#if ((BIG_ENDIAN) || (defined __C51__) || (defined __RC51__) || (defined _CC51))
//! Big Endian Compilers: Bit swapping necessary
#define htole16(x) ((((x) >> 8) & 0x00FF) | (((x) << 8) & 0xFF00))
#define le16toh(x) ((((x) >> 8) & 0x00FF) | (((x) << 8) & 0xFF00))
#elif ((LITTLE_ENDIAN) || (defined __GNUC__) || (defined __clang__) ||(defined SDCC) || (defined HI_TECH_C) || (defined __ICC8051__))
#define htole16(x) (x)
#define le16toh(x) (x)

#else
#error "Compiler not defined. Endian-ness of the compiler cannot be determined."
#endif

/************************** Bit operation macros *****************************/
#define BIT_SET(reg,nbit)                   (reg) |=  (1<<(nbit))
#define BIT_CLR(reg,nbit)                   (reg) &= ~(1<<(nbit))
#define BIT_TGL(reg,nbit)                   (reg) ^=  (1<<(nbit))
#define BIT_CHECK(reg,nbit)                 (((reg) & (1 << (nbit))) >> (nbit))

/*****************************************************************************/

/**
 * @brief TCA9555 register type
 */
typedef uint16_t tca9555_reg_t;

/**
 * @brief TCA9555 register address
 */
typedef enum
{
    TCA9555_REG_ADDR_INPUT = 0x00,
    TCA9555_REG_ADDR_OUTPUT = 0x02,
    TCA9555_REG_ADDR_POLARITY_INV = 0x4,
    TCA9555_REG_ADDR_CONFIGURATION = 0x6,
    TCA9555_REG_ADDR_MAX
} tca9555_reg_addr_t;

/**
 * @brief Check device pointer structure
 *
 * @param device - pointer to device struct
 * @return TCA9555_OK - success
 *         TCA9555_E_NULL_PTR - i2c_read or i2c_write functions is null
 *         TCA9555_E_FAILED - invalid i2c_addr
 */
static tca9555_err_t tca9555_device_check(const tca9555_dev_t *device)
{
    tca9555_err_t rslt = TCA9555_OK;
    if(device == NULL ||
        device->i2c_read == NULL ||
        device->i2c_write == NULL) {
        rslt = TCA9555_E_NULL_PTR;
    }
    if(device->i2c_addr >= TCA9555_ADDR_MAX) {
        rslt = TCA9555_E_FAILED;
    }
    return rslt;
}

/**
 * @brief Read TCA9555 register
 *
 * @param device - pointer to device struct
 * @param reg_addr - read register address
 * @param data - pointer to the register data
 * @return TCA9555_OK - success
 *         TCA9555_E_NULL_PTR - i2c_read or i2c_write functions is null
 *         TCA9555_E_FAILED - invalid device i2c_addr or read register
 */
static tca9555_err_t tca9555_read_reg(const tca9555_dev_t *device,
        tca9555_reg_addr_t reg_addr, tca9555_reg_t *data)
{
    uint16_t rslt = TCA9555_OK;

    rslt = tca9555_device_check(device);
    if(rslt != TCA9555_OK)
        goto exit;

    if(reg_addr >= TCA9555_REG_ADDR_MAX) {
        rslt = TCA9555_E_FAILED;
        goto exit;
    }

    if(data == NULL) {
        rslt = TCA9555_E_NULL_PTR;
        goto exit;
    }

    rslt = device->i2c_read(device->i2c_addr, reg_addr,
            (uint8_t *)data, sizeof(tca9555_reg_t));
    if(rslt != TCA9555_OK) {
        rslt = TCA9555_E_I2C_COM_FAILED;
        goto exit;
    }

    *data = le16toh(*data);

exit:
    return rslt;
}

/**
 * @brief Write TCA9555 register
 *
 * @param device - pointer to device struct
 * @param reg_addr - write register address
 * @param data - pointer to the register data
 * @return TCA9555_OK - success
 *         TCA9555_E_NULL_PTR - i2c_read or i2c_write functions is null
 *         TCA9555_E_FAILED - invalid device i2c_addr or read register
 */
static tca9555_err_t tca9555_write_reg(const tca9555_dev_t *device,
        tca9555_reg_addr_t reg_addr, tca9555_reg_t *data)
{
    uint16_t rslt = TCA9555_OK;

    rslt = tca9555_device_check(device);
    if(rslt != TCA9555_OK)
        goto exit;

    if(reg_addr >= TCA9555_REG_ADDR_MAX) {
        rslt = TCA9555_E_FAILED;
        goto exit;
    }

    if(data == NULL) {
        rslt = TCA9555_E_NULL_PTR;
        goto exit;
    }

    *data = htole16(*data);

    rslt = device->i2c_write(device->i2c_addr, reg_addr,
            (uint8_t *)data, sizeof(tca9555_reg_t));
    if(rslt != TCA9555_OK) {
        rslt = TCA9555_E_I2C_COM_FAILED;
        goto exit;
    }

exit:
    return rslt;
}

/**
 * @brief Initialization of GPIO pin
 *
 * @param device - pointer to device structure
 * @param pin - GPIO pin
 * @param mode - GPIO mode
 * @return TCA9555_OK - success
 *         other - error code from tca9555_err_t enumeration
 */
tca9555_err_t tca9555_gpio_init(tca9555_dev_t *device, tca9555_gpio_pin_t pin,
        tca9555_gpio_mode_t mode)
{
    tca9555_err_t rslt;
    tca9555_reg_t config_register = {0};

    rslt = tca9555_device_check(device);
    if(rslt != TCA9555_OK)
        goto exit;

    if(pin >= TCA9555_GPIO_MAX) {
        rslt = TCA9555_E_INVALID_ARG;
        goto exit;
    }

    if(mode != TCA9555_GPIO_OUTPUT && mode != TCA9555_GPIO_INPUT) {
        rslt = TCA9555_E_INVALID_ARG;
        goto exit;
    }

    rslt = tca9555_read_reg(device, TCA9555_REG_ADDR_CONFIGURATION,
            &config_register);
    if(rslt != TCA9555_OK)
        goto exit;

    if(BIT_CHECK(config_register, pin) != mode) {
        BIT_TGL(config_register, pin);
        rslt = tca9555_write_reg(device, TCA9555_REG_ADDR_CONFIGURATION,
                &config_register);
    }

exit:
    return rslt;
}
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

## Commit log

2024-09-13 Ajout draft shematique
    [Charger.kicad_sch, MoteurProjet_sch.kicad_sch, Moustache.kicad_sch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]
2024-09-13 Correction problemes
    [STM32x.kicad_sch]
2024-09-17 STM32 KiCAD V1
    [Moustache.kicad_sch, STM32x.kicad_sch]
2024-09-18 STM32 KiCAD V2 - 18.09.2024
    [Charger.kicad_sch, MoteurProjet_sch.kicad_sch, Moustache.kicad_sch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]
2024-09-18 KiCAD V3 - 18.09.2024
    [Charger.kicad_sch, Led_Debug.kicad_sch, Moustache.kicad_sch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]
2024-09-20 STM32 KiCAD V4 - 20.09.2024
    [MoteurProjet_sch.kicad_sch, MotorDriver.kicad_sch, STM32x.kicad_sch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]
2024-09-20 STM32 KiCAD V5 - 20.09.2024
    [Charger.kicad_sch, MoteurProjet_sch.kicad_sch, MotorDriver.kicad_sch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]
2024-09-23 Ajout du Read.me de la partie alimentation
2024-09-23 STM32 Template v1(Pins Non-Assigned) - 23.09.2024
2024-09-25 Tests liste de puces
2024-09-25 STM32 KiCAD V5 - 25.09.2024 - Ajout connecteurs TOF, ...
    [Charger.kicad_sch, Led_Debug.kicad_sch, Mecanique.kicad_sch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]
2024-09-25 STM32 KiCAD V6 - 25.09.2024 - Ajout des points test
    [Charger.kicad_sch, MoteurProjet_sch.kicad_sch, STM32x.kicad_sch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]
2024-09-25 STM32 KiCAD V6 - 25.09.2024 - Nettoyage des mauvais pins
    [STM32x.kicad_sch, tom&Jerry_Draft.kicad_sch]
2024-09-25 STM32 KiCAD v7 x CubeIDE - Correction gpio_expander et driver gpio_expander
    [Led_Debug.kicad_sch, tom&Jerry_Draft.kicad_sch]
2024-10-01 STM32 KiCAD v2.0 x CubeIDE - Pin definitif + schematic reviewed
    [Charger.kicad_sch, Led_Debug.kicad_sch, Mecanique.kicad_sch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]
2024-10-02 Adding footprint V0.1
    [Charger.kicad_sch, Led_Debug.kicad_sch, Mecanique.kicad_sch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]
2024-10-02 Changing footprint V0.2
    [Charger.kicad_sch, tof.kicad_sch, tom&Jerry_Draft.kicad_pcb]
2024-10-04 Ajout des bonnes empreintes
    [Charger.kicad_sch, MotorDriver.kicad_sch, tom&Jerry_Draft.kicad_pcb]
2024-10-04 Ajout V2 TOF + MultiPCB Panalize
    [Charger.kicad_sch, Led_Debug.kicad_sch, Mecanique.kicad_sch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]
2024-10-05 Migration CubeIDE vers 1.16.1
    [pcb_tof.kicad_pcb, pcb_tof.kicad_sch]
2024-10-05 First try placement
    [tom&Jerry_Draft.kicad_pcb]
2024-10-05 Try some placement and routing
    [STM32x.kicad_sch, tof.kicad_sch, tom&Jerry_Draft.kicad_pcb]
2024-10-06 Ajout du routage LED + TOF + quelques Via
    [Moustache.kicad_sch, tom&Jerry_Draft.kicad_pcb]
2024-10-06 Ajout des derniers via utiles
    [tom&Jerry_Draft.kicad_pcb]
2024-10-07 Routage Signal Complet
    [Moustache.kicad_sch, STM32x.kicad_sch, tom&Jerry_Draft.kicad_pcb]
2024-10-07 Routage Power
    [tom&Jerry_Draft.kicad_pcb]
2024-10-08 V2.0 placement avec tout dessus
    Aucun routage réalisé
    [Charger.kicad_sch, MotorDriver.kicad_sch, Moustache.kicad_sch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]
2024-10-08 Routage Signal Complet - PCB V2.0
    [Charger.kicad_sch, Led_Debug.kicad_sch, Mecanique.kicad_sch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]
2024-10-08 Corrections mineures routage - PCB V2.0
    [tom&Jerry_Draft.kicad_pcb]
2024-10-09 Routage finish awaiting review PCB2.0
    [tom&Jerry_Draft.kicad_pcb]
2024-10-16 c rémi qui m'a dit
    g écrit sur le PCB.
    [bom.csv, designators.csv, positions.csv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]
2024-10-17 Kicad - Deplacement des pins sous PASTE x empreinte MOSFET
    [BatterieChargingLEDs.kicad_sch, Moustache_out.kicad_sch, tom&Jerry_Draft.kicad_pcb]
2024-10-17 Nothing important, just an inchident
    [BatterieChargingLEDs.kicad_sch, Charger.kicad_sch]
2024-10-21 Cleaning for PCB prof review
    [BatterieChargingLEDs.kicad_sch, Charger.kicad_sch, Led_Debug.kicad_sch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]
2024-10-21 Correction erreurs PCB
    [Tom&Jerry_PCB.kicad_pcb]
2024-10-22 Adding all files to critic error PCB
    [Charger.kicad_sch, Led_Debug.kicad_sch, Mecanique.kicad_sch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]
2024-10-23 Last commit before PCB command
    [Tom&Jerry_PCB.kicad_pcb]
2024-10-23 Generation des jlcpcb files
    [bom.csv, designators.csv, positions.csv]
2024-10-23 Rshunt en 0603
    [bom.csv, positions.csv]
2024-10-23 Derniere modif jlcpcb
    [MotorDriver.kicad_sch, Tom&Jerry_PCB.kicad_pcb, bom.csv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]
2024-11-20 MAJOR UPGRADE : cubeIDE rtos - multiple drivers work | MINOR UPGRADE : schematic correction (too late)| COMMIT BEFORE MULTIPLE TASKS CREATION
    [Charger.kicad_sch, Moustache.kicad_sch, musique.kicad_sch]
2024-11-26 Changement et MAJ des README electronique
2024-12-11 Chat en cours de miaulement
2024-12-13 Moteurs controlés par Lidar : OK (mode:chat only)
2025-01-09 ReadMe Lidar
2025-01-10 Ajout bonne bobines + 3.3v gpio expander + Driver moteur
    [Moustache.kicad_sch, STM32x.kicad_sch, Tom&Jerry_PCB.kicad_pcb]
2025-01-10 VERSION VF.1| Ajout d'un -v sur la commande angle pour eviter de flood le temrinal

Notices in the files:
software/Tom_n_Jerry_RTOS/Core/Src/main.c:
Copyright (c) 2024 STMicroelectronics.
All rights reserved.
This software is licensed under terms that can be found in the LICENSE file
